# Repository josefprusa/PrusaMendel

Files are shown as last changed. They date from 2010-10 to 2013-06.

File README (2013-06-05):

Prusa Mendel iteration 2

This is second big change, formerly known as felt branch.
Released 11.11.11 :-)

Please read http://reprap.org/wiki/Prusa_Mendel before attempting to build this. There is also PDF (manual-wiki) with backup documentation from reprap.org.  

Imported stuff:
Extruder by Greg Frost
Parametric Involute Bevel and Spur Gears by GregFrost
Belt pulley is http://www.thingiverse.com/thing:3104 by GilesBathgate

Prusa Mendel part list:

To print (not including the extruder drive):

4x frame-vertex-with-foot
2x frame-vertex-without-foot
2x coupling
1x x-carriage
1x x-end-idler
1x x-end-motor
2x z-motor-mount
4x belt-clamp
2x belt-clamp-nut-holder
8x bar-clamp
2x rod-clamp
1x y-motor-bracket
3x y-bushing
3x endstop-holder

X90390893??°03I

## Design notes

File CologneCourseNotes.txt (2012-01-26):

M8 nut trap on the wade big gear is toooooo big
-> caused by the M8 nut set toooo big because of the compatibility with 5/16
--> but the wade bolts are all M8 so I need to introduce new variable in the settings

M3 nut traps in gregstruder are tooo small
-> introduce the M3 nut size for not melting in

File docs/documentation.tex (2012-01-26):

\documentclass[11pt]{article}
\usepackage[latin2]{inputenc}
\usepackage{a4wide}
\usepackage{graphicx}
\usepackage{hyperref}
\hypersetup{colorlinks=true,linkcolor=blue}
\title{Prusa Mendel iteration 2 Documentation}
\author{ThingDoc}

\begin{document}

\maketitle
\begin{center}
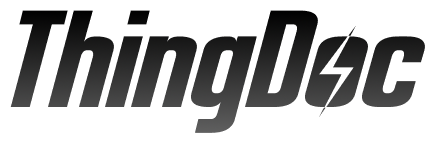
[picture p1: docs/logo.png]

\end{center}
Prusa Mendel is simplified version of Mendel form RepRap project. RepRap is open source 3D printer.

\newpage

\tableofcontents

\newpage

\section{Bill of Materials}
List of things you need to build the machine divided by categories.

\subsection{Rods and Bars}
\begin{itemize}
\item 1x \hyperlink{thing_idler-m8-piece}{Idler}
\end{itemize}

\subsection{Nuts\&bolts}
\begin{itemize}
\item 3x 608 skate bearing
\item 4x M4 nut
\item 3x M3 10mm screw
\item 2x M4 25mm screw
\item 1x \hyperlink{thing_hobbed-bolt}{M8 hobbed bolt}
\item 8x M3 15mm screw with HEX head
\item 2x M3 10mm screw with hex head
\item 1x M3 25mm screw
\item 1x M3 grub screw
\item 2x M3 25mm screw with HEX head
\item 12x M3 nut
\item 73x M8 washer
\item 74x M8 nut
\item 29x M3 washer
\item 1x M3 10mm screw with flat head
\item 2x M3 40mm screw
\end{itemize}

\subsection{Printed}
\begin{itemize}
\item 1x \hyperlink{thing_extruder-body}{Extruder body}
\item 8x \hyperlink{thing_bar-clamp}{Bar clamp}
\item 4x \hyperlink{thing_y-bushing}{Y bushing}
\item 2x \hyperlink{thing_frame-vertex}{Frame vertex}
\item 1x \hyperlink{thing_large-gear}{Large extruder gear}
\item 1x \hyperlink{thing_small-gear}{Small extruder gear}
\item 2x \hyperlink{thing_rod-clamp}{Rod clamp}
\item 4x \hyperlink{thing_frame-vertex-foot}{Frame vertex with foot}
\item 1x \hyperlink{thing_y-motor-bracket}{Y motor bracket}
\item 2x \hyperlink{thing_belt-clamp}{Belt clamp}
\item 1x \hyperlink{thing_x-carriage}{X carriage}
\item 1x \hyperlink{thing_z-motor-mount}{Z motor mount}
\item 1x \hyperlink{thing_idler}{Extruder Idler}
\end{itemize}

\newpage

\section{Things Overview}
List of things and their descriptions.

\hypertarget{thing_coupling-tube}{\subsection{Coupling tube}}
20mm long piece of PVC tube. 5mm inside diameter, 8mm outside diameter.

\hypertarget{thing_frame-triangle}{\subsection{Frame triangle}}
Two triangle parts which will later form a frame.

\hypertarget{thing_frame-with-axes}{\subsection{Frame with axes}}
Frame with all axes mounted

\hypertarget{thing_frame-vertex}{\subsection{Frame vertex}}
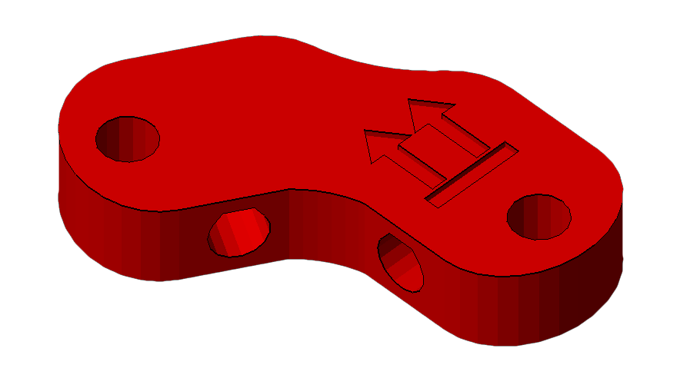
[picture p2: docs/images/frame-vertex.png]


\hypertarget{thing_frame}{\subsection{Frame}}
Frame for adding all of the other parts
There is a triangle on each side of the Prusa RepRap. You will need to make two of these and then connect them together (in the next steps) to form the Prusa frame. Each side is an equilateral triangle with a frame vertex on each corner. You can use either footed or non-footed vertices to build this. (The footed ones look better, but are not critical.) The instructions assume you are using footed vertices.

\hypertarget{thing_y-motor-bracket}{\subsection{Y motor bracket}}
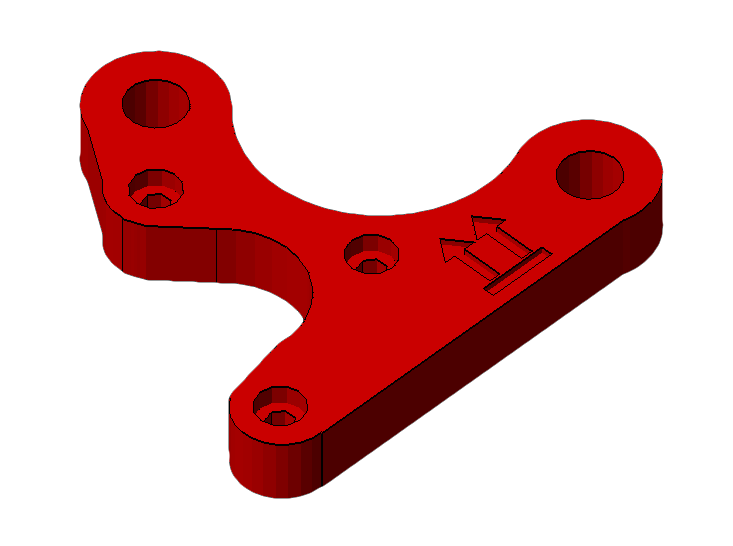
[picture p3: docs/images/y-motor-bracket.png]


\hypertarget{thing_belt-clamp}{\subsection{Belt clamp}}
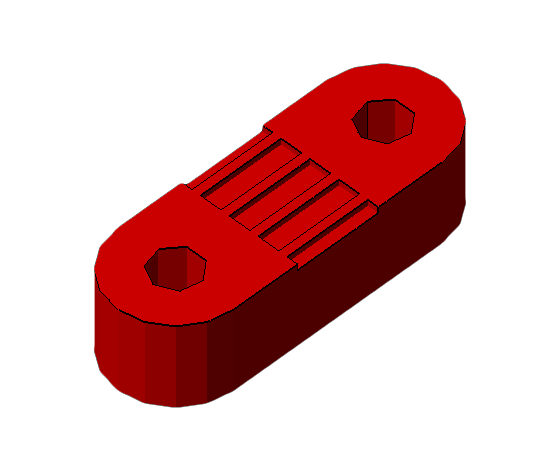
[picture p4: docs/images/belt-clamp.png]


\hypertarget{thing_hobbed-bolt}{\subsection{M8 hobbed bolt}}

\hypertarget{thing_idler}{\subsection{Extruder Idler}}
Extruder idler

\hypertarget{thing_frame-with-y}{\subsection{Frame with Y axis}}
Frame with Y axis mounted

\hypertarget{thing_y-bushing}{\subsection{Y bushing}}

\hypertarget{thing_large-gear-assembly}{\subsection{Large extruder gear assembly}}

\hypertarget{thing_bar-clamp}{\subsection{Bar clamp}}
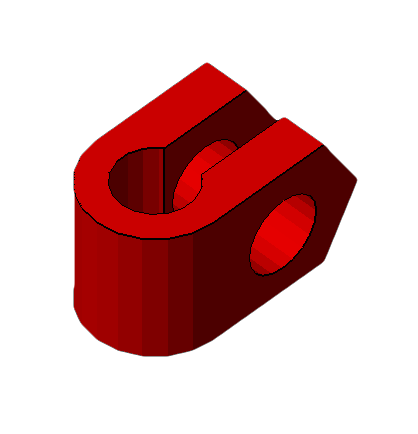
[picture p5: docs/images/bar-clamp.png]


\hypertarget{thing_xz-axis}{\subsection{XZ axis}}
Assembled XZ axis

\hypertarget{thing_large-gear}{\subsection{Large extruder gear}}

\hypertarget{thing_frame-vertex-foot}{\subsection{Frame vertex with foot}}
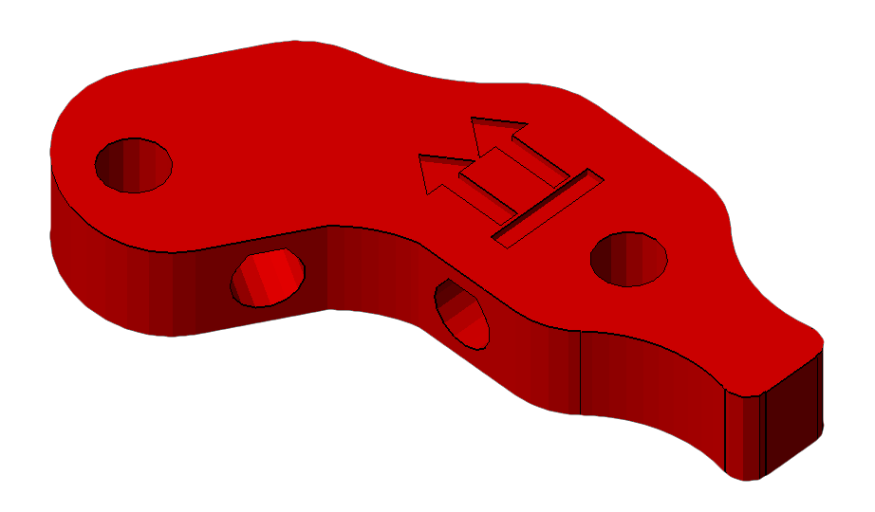
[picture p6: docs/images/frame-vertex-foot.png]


\hypertarget{thing_x-end-motor}{\subsection{X end motor}}

\hypertarget{thing_extruder-body}{\subsection{Extruder body}}
Extruder body

\hypertarget{thing_small-gear}{\subsection{Small extruder gear}}

\hypertarget{thing_extruder-spring}{\subsection{Extruder spring}}
Spring used for idler on extruder.

\hypertarget{thing_printable-bushing}{\subsection{Printable Bushing}}

\hypertarget{thing_x-carriage}{\subsection{X carriage}}
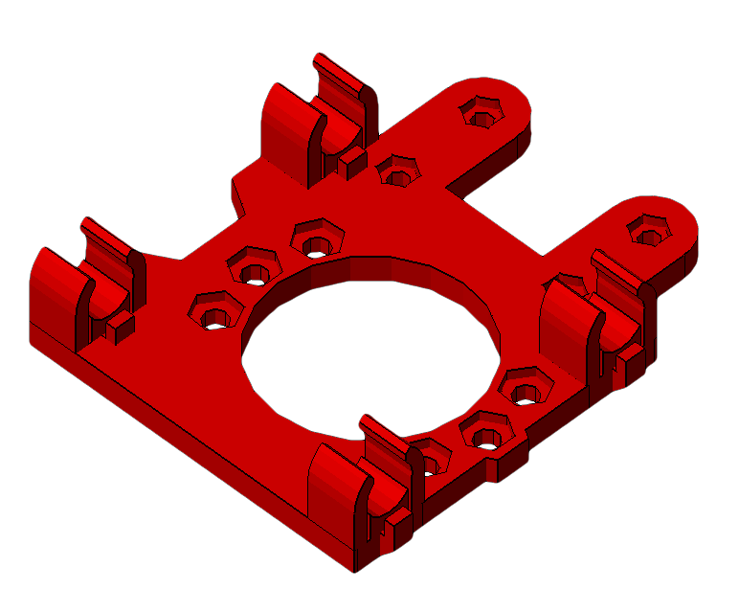
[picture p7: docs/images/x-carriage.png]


\hypertarget{thing_x-end-idler}{\subsection{X end idler}}

\hypertarget{thing_rod-clamp}{\subsection{Rod clamp}}
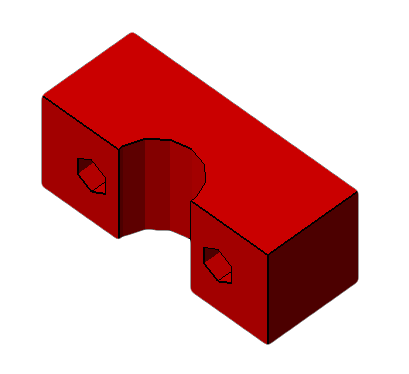
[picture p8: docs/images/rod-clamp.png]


\hypertarget{thing_z-motor-mount}{\subsection{Z motor mount}}
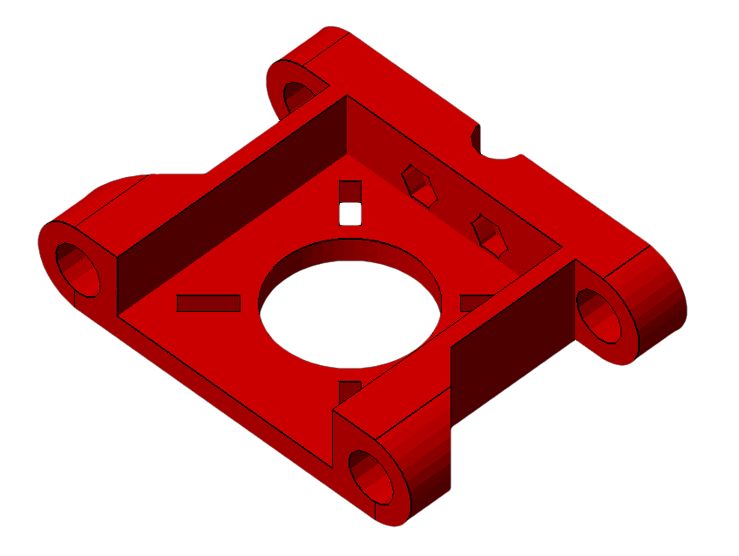
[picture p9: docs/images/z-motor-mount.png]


\hypertarget{thing_endstop-holder}{\subsection{Endstop holder}}

\hypertarget{thing_bushing}{\subsection{Bushing}}

\hypertarget{thing_idler-m8-piece}{\subsection{Idler}}
Small M8 rod

\hypertarget{thing_pulley}{\subsection{Pulley}}

\hypertarget{thing_coupling}{\subsection{Coupling}}

\hypertarget{thing_y-axis}{\subsection{Y axis}}
Assembled Y axis

\hypertarget{thing_bearing-guide}{\subsection{Bearing guide}}
Helps to hold belt aligned on the bearing.

\hypertarget{thing_cleaned-extruder-body}{\subsection{Clenaed xtruder body}}
Cleaned extruder body

\hypertarget{thing_carriage}{\subsection{Carriage}}
X-carriage with mounted extruder

\hypertarget{thing_extruder}{\subsection{Extruder}}
Extruder

\newpage

\section{Assembly Instructions}

\subsection{Assemble M8 hobbed bolt}Steps:
\begin{enumerate}
\item Use thread cutting bit in electric screwdriver ...
\end{enumerate}

\subsection{Assemble Large extruder gear assembly}
Things needed:
\begin{itemize}
\item 1x \hyperlink{thing_large-gear}{Large extruder gear}
\item 1x \hyperlink{thing_hobbed-bolt}{M8 hobbed bolt}
\end{itemize}
Steps:
\begin{enumerate}
\item Insert hobbed bolt into main hole.
\item Add some M8 washers from other side, later with their count you adjust position of hobbed part in filament path.
\end{enumerate}

\subsection{Assemble Small extruder gear}
Things needed:
\begin{itemize}
\item 1x M3 nut
\item 1x M3 grub screw
\end{itemize}
Steps:
\begin{enumerate}
\item Insert nut into cavity in printed gear.
\item Tighten the grub screw a bit, just to hold in place.
\end{enumerate}

\subsection{Assemble Clenaed xtruder body}
Things needed:
\begin{itemize}
\item 1x \hyperlink{thing_extruder-body}{Extruder body}
\end{itemize}
Steps:
\begin{enumerate}
\item Clean all the supports from the part.
\item One blocks the hole in the middle of the axis and one supports the part later making hinge for idler.
\end{enumerate}

\subsection{Assemble Extruder Idler}
Things needed:
\begin{itemize}
\item 1x 608 skate bearing
\item 1x \hyperlink{thing_idler-m8-piece}{Idler}
\end{itemize}
Steps:
\begin{enumerate}
\item Insert piece of M8 rod into bearing.
\item Insert 608 bearing with rod into printed idler part.
\end{enumerate}

\subsection{Assemble Extruder}
Things needed:
\begin{itemize}
\item 2x 608 skate bearing
\item 2x M4 nut
\item 3x M3 10mm screw
\item 1x \hyperlink{thing_large-gear-assembly}{Large extruder gear assembly}
\item 1x NEMA17 stepper motor
\item 1x \hyperlink{thing_small-gear}{Small extruder gear}
\item 1x \hyperlink{thing_cleaned-extruder-body}{Clenaed xtruder body}
\item 2x M3 40mm screw
\item 8x M3 washer
\item 1x M8 washer
\item 1x \hyperlink{thing_idler}{Extruder Idler}
\item 1x M3 nut
\item 1x M3 25mm screw
\item 2x \hyperlink{thing_extruder-spring}{Extruder spring}
\item 2x M8 nut
\end{itemize}
Steps:
\begin{enumerate}
\item Take idler and insert nut into small nut-trap inside the hinge.
\item While holding the nut in place, preprare M3x25 bolt with washer and screw it into the hinge just enough to hold the nut.
\item Now take the extruder body and idler. Place idler on the hinge counterpart and compleately screw the M3x25 bolt. This will create secured hinge.
\item Place M4 nuts into their nut traps, secure them with piece of tape. We need them in place, since later they would be harder to access.
\item Prepare your NEMA17 stepper motor and three M3x10 screws with washers.
\item Hold motor on place and lightly tighten the screws. We need to adjust motor position later, no need to tighten it hard.
\item Place two skate bearings on ther position, they should snuggly fit in.
\item Insert prepared large gear into the body with mounted bearings.
\item Check if the alignment of hobbed part with the filament path. Adjust it accordingly with adding or removing M8 washers.
\item After adjusting, we need to fix the bolt in. So we place washer at the end of hobbed bolt and with two M8 nuts we will do locknut by tightening them against each other.
\item Check if large gear turns freely.
\item Prepare two M3x40 screws with sandwitch of washer-spring-washer.
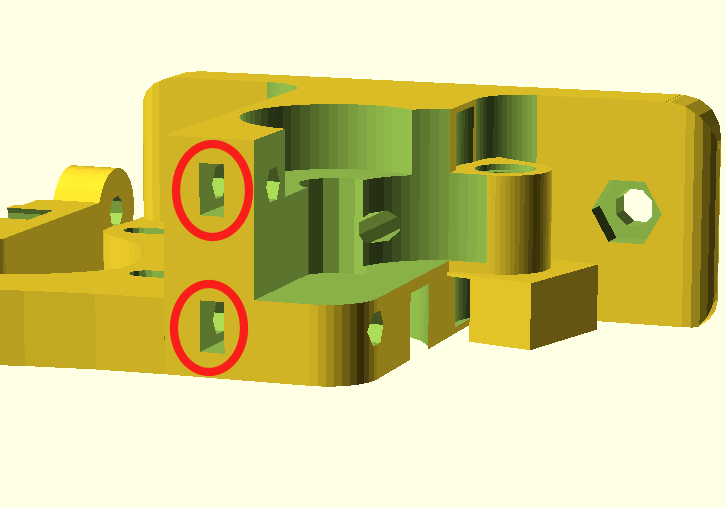
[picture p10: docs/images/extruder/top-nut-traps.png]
\item Insert two M3 nuts into nut traps on top of drive mechanism.\\ 
\item Insert prepared screws into the holes on idler. Close the idler and tighten the screws into the trapped nuts. More you tighten those screws, more pressure will be on fillament.
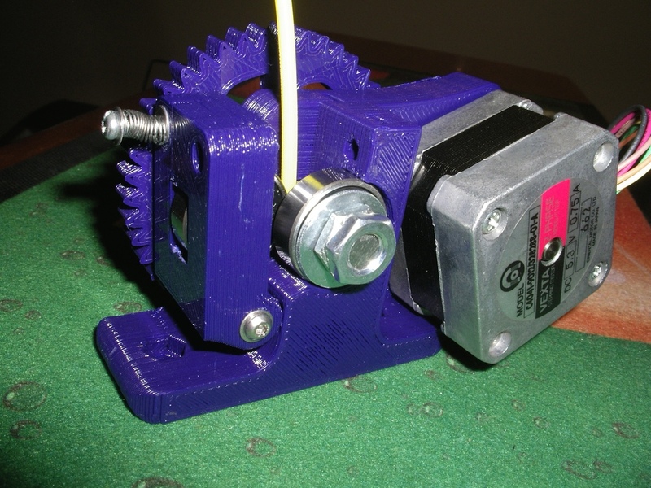
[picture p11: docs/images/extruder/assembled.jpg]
\item Your extruder is done.\\ 
\end{enumerate}

\subsection{Assemble Frame triangle}
Things needed:
\begin{itemize}
\item 1x \hyperlink{thing_bar-clamp}{Bar clamp}
\item 1x \hyperlink{thing_frame-vertex}{Frame vertex}
\item 2x \hyperlink{thing_frame-vertex-foot}{Frame vertex with foot}
\end{itemize}
Steps:
\begin{enumerate}
\item Take one of the 370mm threaded rods, and slip an M8 washer onto the middle of it.
\item Take the RP bar clamp (the U-shaped bit with the two holes) and slide the threaded rod through the two holes until the clamp sits next to the washer.
\item Slide another washer onto the rod from the other side.
\item Thread two M8 nuts onto either side of the clamp, until they are next to the washer, but do not tighten them yet.
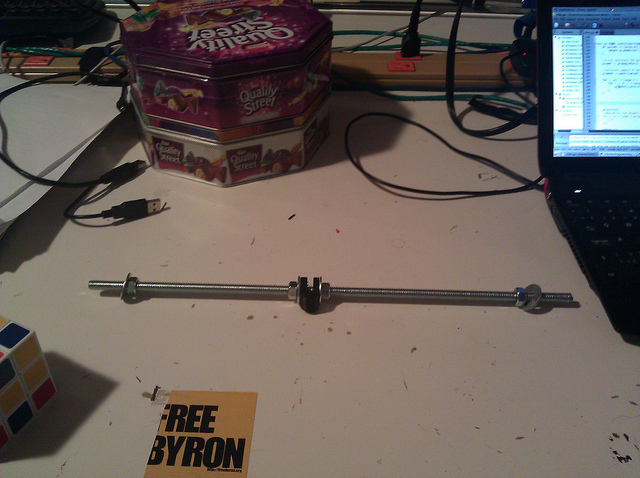
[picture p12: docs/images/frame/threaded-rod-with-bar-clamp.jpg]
\item Thread another two nuts on each side of the rod, followed by washers. See the picture for what it should look like.\\ 
\item The bar clamp on the threaded rod.
\item Slide the rod through the wider bottom (footed) side of two vertices. Make sure the feet point in the same direction, and the bulge on the non-footed sides of the vertices point outwards.
\item Place another washer and nut on the other side of the vertex. Tighten, but not too much. We'll need a bit of flexibility here still.
\item Take another 370mm M8 threaded rod and place a nut followed by a washer at each end.
\item Place one end of the threaded rod into the one of the two footed frame vertices. It should be in the same plane as the first threaded rod. Fix it in place with a washer and nut. You should now have two sides of the equilateral triangle.
\item Take the third piece of threaded rod and put a nut and washer on each end. Place it in the other footed vertex and fix it in place with a washer and nut. You should now have a triangle of threaded rods with two footed vertices on two of the corners, nothing in the third corner, and a bar clamp between the two vertices.
\item Take the third vertex (non-footed) and slide it onto the threaded rods in the final corner of the triangle.
\item Move all the nuts on the end of the rods to the exact end of the rod. Tighten all the inner nuts. This way, no measurement is needed.
\item You should now have a sturdy triangle with equal-length sides, two feet on the bottom, and a bar clamp between the feet. Adjust the nuts around the bar clamp (but do not crush the bar clamp together yet) until it's approximately in the middle of the rod. Leave the nuts there loose. See the photo for what you should have at this point.
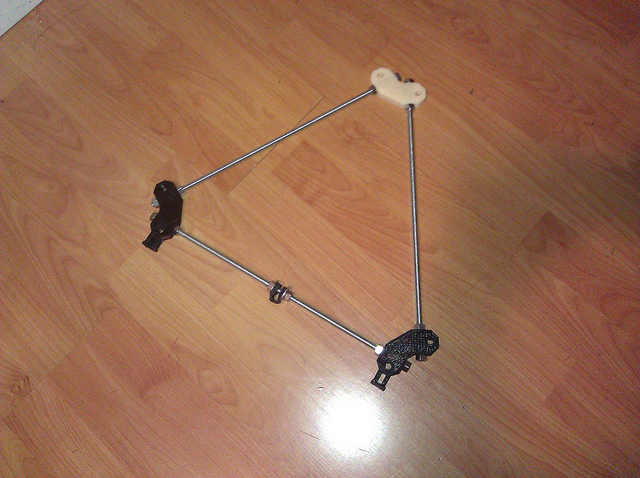
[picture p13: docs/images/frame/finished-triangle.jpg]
\item That's it, that's one of the triangles done. Repeat the entire procedure for the second triangle. It is identical to the first.\\ 
\end{enumerate}

\subsection{Assemble Prusa Mendel iteration 2}
Things needed:
\begin{itemize}
\item 1x \hyperlink{thing_carriage}{Carriage}
\item 1x \hyperlink{thing_frame-with-axes}{Frame with axes}
\end{itemize}
Steps:
\begin{enumerate}
\item Assembly info
\end{enumerate}

\newpage

\end{document}

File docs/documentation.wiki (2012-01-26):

== Bill of Materials ==

=== Rods and Bars ===
{| class="wikitable sortable" border="1"
|-
! scope="col" | Quantity
! scope="col" | Description
! scope="col" | Type
! scope="col" class="unsortable" | Comments
! scope="col" class="unsortable" | Diagram
|-
| 1 || Idler ||  ||  ||
|}

=== Nuts&bolts ===
{| class="wikitable sortable" border="1"
|-
! scope="col" | Quantity
! scope="col" | Description
! scope="col" | Type
! scope="col" class="unsortable" | Comments
! scope="col" class="unsortable" | Diagram
|-
| 3 || 608 skate bearing ||  ||  || 50px
|-
| 4 || M4 nut ||  ||  ||
|-
| 3 || M3 10mm screw ||  ||  ||
|-
| 2 || M4 25mm screw ||  ||  ||
|-
| 1 || M8 hobbed bolt ||  ||  ||
|-
| 8 || M3 15mm screw with HEX head ||  ||  ||
|-
| 2 || M3 10mm screw with hex head ||  ||  ||
|-
| 1 || M3 25mm screw ||  ||  ||
|-
| 1 || M3 grub screw ||  ||  ||
|-
| 2 || M3 25mm screw with HEX head ||  ||  ||
|-
| 12 || M3 nut ||  ||  ||
|-
| 73 || M8 washer ||  ||  ||
|-
| 74 || M8 nut ||  ||  ||
|-
| 29 || M3 washer ||  ||  ||
|-
| 1 || M3 10mm screw with flat head ||  ||  ||
|-
| 2 || M3 40mm screw ||  ||  ||
|}

=== Printed ===
{| class="wikitable sortable" border="1"
|-
! scope="col" | Quantity
! scope="col" | Description
! scope="col" | Type
! scope="col" class="unsortable" | Comments
! scope="col" class="unsortable" | Diagram
|-
| 1 || Extruder body ||  ||  ||
|-
| 8 || Bar clamp ||  ||  || 50px
|-
| 4 || Y bushing ||  ||  ||
|-
| 2 || Frame vertex ||  ||  || 50px
|-
| 1 || Large extruder gear ||  ||  ||
|-
| 1 || Small extruder gear ||  ||  ||
|-
| 2 || Rod clamp ||  ||  || 50px
|-
| 4 || Frame vertex with foot ||  ||  || 50px
|-
| 1 || Y motor bracket ||  ||  || 50px
|-
| 2 || Belt clamp ||  ||  || 50px
|-
| 1 || X carriage ||  ||  || 50px
|-
| 1 || Z motor mount ||  ||  || 50px
|-
| 1 || Extruder Idler ||  ||  ||
|}

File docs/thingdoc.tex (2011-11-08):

\documentclass[11pt]{article}
\usepackage[latin2]{inputenc}
\usepackage{a4wide}
\usepackage{graphicx}
\usepackage{hyperref}
\hypersetup{colorlinks=true,linkcolor=blue}
\title{Prusa Mendel generation 2 Documentation}
\author{ThingDoc}

\begin{document}

\maketitle
\begin{center}

\end{center}
Prusa Mendel is simplified version of Mendel form RepRap project. RepRap is open source 3D printer.

\newpage

\tableofcontents

\newpage

\section{Bill of Materials}
List of things you need to build the machine divided by categories.

\subsection{Rods and Bars}
\begin{itemize}
\item 1x \hyperlink{thing_idler-m8-piece}{Idler}
\end{itemize}

\subsection{Nuts\&bolts}
\begin{itemize}
\item 3x 608 skate bearing
\item 4x M4 nut
\item 3x M3 10mm screw
\item 2x M4 25mm screw
\item 1x \hyperlink{thing_hobbed-bolt}{M8 hobbed bolt}
\item 8x M3 15mm screw with HEX head
\item 2x M3 10mm screw with hex head
\item 1x M3 25mm screw
\item 1x M3 grub screw
\item 2x M3 25mm screw with HEX head
\item 12x M3 nut
\item 73x M8 washer
\item 74x M8 nut
\item 29x M3 washer
\item 1x M3 10mm screw with flat head
\item 2x M3 40mm screw
\end{itemize}

\subsection{Printed}
\begin{itemize}
\item 1x \hyperlink{thing_extruder-body}{Extruder body}
\item 8x \hyperlink{thing_bar-clamp}{Bar clamp}
\item 4x \hyperlink{thing_y-bushing}{Y bushing}
\item 2x \hyperlink{thing_frame-vertex}{Frame vertex}
\item 1x \hyperlink{thing_y-motor-bracket}{Y motor bracket}
\item 1x \hyperlink{thing_small-gear}{Small extruder gear}
\item 2x \hyperlink{thing_rod-clamp}{Rod clamp}
\item 4x \hyperlink{thing_frame-vertex-foot}{Frame vertex with foot}
\item 1x \hyperlink{thing_large-gear}{Large extruder gear}
\item 2x \hyperlink{thing_belt-clamp}{Belt clamp}
\item 1x \hyperlink{thing_idler}{Extruder Idler}
\item 1x \hyperlink{thing_z-motor-mount}{Z motor mount}
\item 1x \hyperlink{thing_x-carriage}{X carriage}
\end{itemize}

\newpage

\section{Things Overview}
List of things and their descriptions.

\hypertarget{thing_coupling-tube}{\subsection{Coupling tube}}
20mm long piece of PVC tube. 5mm inside diameter, 8mm outside diameter.

\hypertarget{thing_frame-triangle}{\subsection{Frame triangle}}
Two triangle parts which will later form a frame.

\hypertarget{thing_y-axis}{\subsection{Y axis}}
Assembled Y axis

\hypertarget{thing_frame-with-axes}{\subsection{Frame with axes}}
Frame with all axes mounted

\hypertarget{thing_frame-vertex}{\subsection{Frame vertex}}


\hypertarget{thing_frame}{\subsection{Frame}}
Frame for adding all of the other parts
There is a triangle on each side of the Prusa RepRap. You will need to make two of these and then connect them together (in the next steps) to form the Prusa frame. Each side is an equilateral triangle with a frame vertex on each corner. You can use either footed or non-footed vertices to build this. (The footed ones look better, but are not critical.) The instructions assume you are using footed vertices.

\hypertarget{thing_y-motor-bracket}{\subsection{Y motor bracket}}


\hypertarget{thing_belt-clamp}{\subsection{Belt clamp}}


\hypertarget{thing_hobbed-bolt}{\subsection{M8 hobbed bolt}}

\hypertarget{thing_idler}{\subsection{Extruder Idler}}
Extruder idler

\hypertarget{thing_frame-with-y}{\subsection{Frame with Y axis}}
Frame with Y axis mounted

\hypertarget{thing_y-bushing}{\subsection{Y bushing}}

\hypertarget{thing_bar-clamp}{\subsection{Bar clamp}}


\hypertarget{thing_calibration}{\subsection{Configuration test}}

\hypertarget{thing_xz-axis}{\subsection{XZ axis}}
Assembled XZ axis

\hypertarget{thing_large-gear}{\subsection{Large extruder gear}}

\hypertarget{thing_frame-vertex-foot}{\subsection{Frame vertex with foot}}

\hypertarget{thing_x-end-motor}{\subsection{X end motor}}

\hypertarget{thing_extruder-body}{\subsection{Extruder body}}
Extruder body

\hypertarget{thing_small-gear}{\subsection{Small extruder gear}}

\hypertarget{thing_extruder-spring}{\subsection{Extruder spring}}
Spring used for idler on extruder.

\hypertarget{thing_printable-bushing}{\subsection{Printable Bushing}}

\hypertarget{thing_x-carriage}{\subsection{X carriage}}


\hypertarget{thing_x-end-idler}{\subsection{X end idler}}

\hypertarget{thing_rod-clamp}{\subsection{Rod clamp}}


\hypertarget{thing_z-motor-mount}{\subsection{Z motor mount}}


\hypertarget{thing_endstop-holder}{\subsection{Endstop holder}}

\hypertarget{thing_bushing}{\subsection{Bushing}}

\hypertarget{thing_idler-m8-piece}{\subsection{Idler}}
Small M8 rod

\hypertarget{thing_pulley}{\subsection{Pulley}}

\hypertarget{thing_coupling}{\subsection{Coupling}}

\hypertarget{thing_bearing-guide}{\subsection{Bearing guide}}
Helps to hold belt aligned on the bearing.

\hypertarget{thing_carriage}{\subsection{Carriage}}
X-carriage with mounted extruder

\hypertarget{thing_extruder}{\subsection{Extruder}}
Extruder

\newpage

\section{Assembly Instructions}

\subsection{Assemble Small extruder gear}
Things needed:
\begin{itemize}
\item 1x M3 nut
\item 1x M3 grub screw
\end{itemize}
Steps:
\begin{enumerate}
\item Insert nut into cavity in printed gear.
\item Tighten the grub screw a bit, just to hold in place.
\end{enumerate}

\subsection{Assemble M8 hobbed bolt}Steps:
\begin{enumerate}
\item Use thread cutting bit in electric screwdriver ...
\end{enumerate}

\subsection{Assemble Large extruder gear}
Things needed:
\begin{itemize}
\item 1x \hyperlink{thing_hobbed-bolt}{M8 hobbed bolt}
\end{itemize}
Steps:
\begin{enumerate}
\item Insert hobbed bolt into main hole.
\item Add some M8 washers from other side, later with their count you adjust position of hobbed part in filament path.
\end{enumerate}

\subsection{Assemble Extruder Idler}
Things needed:
\begin{itemize}
\item 1x 608 skate bearing
\item 1x \hyperlink{thing_idler-m8-piece}{Idler}
\end{itemize}
Steps:
\begin{enumerate}
\item Insert piece of M8 rod into bearing.
\item Insert 608 bearing with rod into printed idler part.
\end{enumerate}

\subsection{Assemble Extruder}
Things needed:
\begin{itemize}
\item 2x 608 skate bearing
\item 1x \hyperlink{thing_extruder-body}{Extruder body}
\item 3x M3 10mm screw
\item 2x M4 nut
\item 1x \hyperlink{thing_small-gear}{Small extruder gear}
\item 1x M3 25mm screw
\item 1x NEMA17 stepper motor
\item 1x \hyperlink{thing_large-gear}{Large extruder gear}
\item 8x M3 washer
\item 1x M8 washer
\item 1x \hyperlink{thing_idler}{Extruder Idler}
\item 1x M3 nut
\item 2x M3 40mm screw
\item 2x \hyperlink{thing_extruder-spring}{Extruder spring}
\item 2x M8 nut
\end{itemize}
Steps:
\begin{enumerate}
\item Take idler and insert nut into small nut-trap inside the hinge.
\item While holding the nut in place, preprare M3x25 bolt with washer and screw it into the hinge just enough to hold the nut.
\item Now take the extruder body and idler. Place idler on the hinge counterpart and compleately screw the M3x25 bolt. This will create secured hinge.
\item Place M4 nuts into their nut traps, secure them with piece of tape. We need them in place, since later they would be harder to access.
\item Prepare your NEMA17 stepper motor and three M3x10 screws with washers.
\item Hold motor on place and lightly tighten the screws. We need to adjust motor position later, no need to tighten it hard.
\item Place two skate bearings on ther position, they should snuggly fit in.
\item Insert prepared large gear into the body with mounted bearings.
\item Check if the alignment of hobbed part with the filament path. Adjust it accordingly with adding or removing M8 washers.
\item After adjusting, we need to fix the bolt in. So we place washer at the end of hobbed bolt and with two M8 nuts we will do locknut by tightening them against each other.
\item Check if large gear turns freely.
\item Prepare two M3x40 screws with sandwitch of washer-spring-washer.
\item Insert two M3 nuts into nut traps on top of drive mechanism.\\ 
\item Insert prepared screws into the holes on idler. Close the idler and tighten the screws into the trapped nuts. More you tighten those screws, more pressure will be on fillament.
\item Your extruder is done.\\ 
\end{enumerate}

\subsection{Assemble Frame triangle}
Things needed:
\begin{itemize}
\item 1x \hyperlink{thing_bar-clamp}{Bar clamp}
\item 1x \hyperlink{thing_frame-vertex}{Frame vertex}
\item 2x \hyperlink{thing_frame-vertex-foot}{Frame vertex with foot}
\end{itemize}
Steps:
\begin{enumerate}
\item Take one of the 370mm threaded rods, and slip an M8 washer onto the middle of it.
\item Take the RP bar clamp (the U-shaped bit with the two holes) and slide the threaded rod through the two holes until the clamp sits next to the washer.
\item Slide another washer onto the rod from the other side.
\item Thread two M8 nuts onto either side of the clamp, until they are next to the washer, but do not tighten them yet.
\item Thread another two nuts on each side of the rod, followed by washers. See the picture for what it should look like.\\ 
\item The bar clamp on the threaded rod.
\item Slide the rod through the wider bottom (footed) side of two vertices. Make sure the feet point in the same direction, and the bulge on the non-footed sides of the vertices point outwards.
\item Measure the distance. The distance between the two vertices should be 290mm (along the rod, equivalent is 11-13/32"). Get it approximately right now, we will check this again later. If you have a frame jig, place it between the two vertices and adjust the nuts until you can just barely fit the jig J1 between them.
\item Place another washer and nut on the other side of the vertex. Tighten, but not too much. We'll need a bit of flexibility here still.
\item Take another 370mm M8 threaded rod and place a nut followed by a washer at each end.
\item Place one end of the threaded rod into the one of the two footed frame vertices. It should be in the same plane as the first threaded rod. Fix it in place with a washer and nut. You should now have two sides of the equilateral triangle.
\item Take the third piece of threaded rod and put a nut and washer on each end. Place it in the other footed vertex and fix it in place with a washer and nut. You should now have a triangle of threaded rods with two footed vertices on two of the corners, nothing in the third corner, and a bar clamp between the two vertices.
\item Take the third vertex (non-footed) and slide it onto the threaded rods in the final corner of the triangle. Measure the lengths of the three sides to make sure they are all 290mm long (along the rod from plastic part to plastic part, equivalent is 11-13/32"). Adjust the nuts to make sure this is so. Use the frame jig J1 if you have one. Once done, place a washer and nut on each of the two rods at the top of the vertex. Tighten all the outer nuts.
\item The finished frame triangle
\item You should now have a sturdy triangle with equal-length sides, two feet on the bottom, and a bar clamp between the feet. Adjust the nuts around the bar clamp (but do not crush the bar clamp together yet) until it's approximately in the middle of the rod. Leave the nuts there loose. See the photo for what you should have at this point.
\item That's it, that's one of the triangles done. Repeat the entire procedure for the second triangle. It is identical to the first.\\ 
\end{enumerate}

\subsection{Assemble Prusa Mendel generation 2}
Things needed:
\begin{itemize}
\item 1x \hyperlink{thing_carriage}{Carriage}
\item 1x \hyperlink{thing_frame-with-axes}{Frame with axes}
\end{itemize}
Steps:
\begin{enumerate}
\item Assembly info
\end{enumerate}

\newpage

\end{document}

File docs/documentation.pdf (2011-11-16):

## Prusa Mendel iteration 2 Documentation

ThingDoc

November 16, 2011

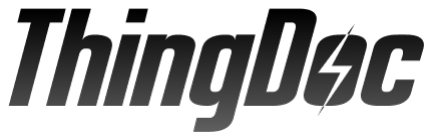
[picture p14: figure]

Prusa Mendel is simplified version of Mendel form RepRap project. RepRap is open source 3D printer.

## Contents

## 1 Bill of Materials

List of things you need to build the machine divided by categories.

### 1.1 Rods and Bars

- 1x Idler

### 1.2 Nuts&bolts

- 3x 608 skate bearing
- 4x M4 nut
- 3x M3 10mm screw
- 2x M4 25mm screw
- 1x M8 hobbed bolt
- 8x M3 15mm screw with HEX head
- 2x M3 10mm screw with hex head
- 1x M3 25mm screw
- 1x M3 grub screw
- 2x M3 25mm screw with HEX head
- 12x M3 nut
- 73x M8 washer
- 74x M8 nut
- 29x M3 washer
- 1x M3 10mm screw with flat head
- 2x M3 40mm screw

### 1.3 Printed

- 1x Extruder body
- 8x Bar clamp
- 4x Y bushing
- 2x Frame vertex
- 1x Y motor bracket
- 1x Small extruder gear

- 2x Rod clamp
- 4x Frame vertex with foot
- 1x Large extruder gear
- 2x Belt clamp
- 1x Extruder Idler
- 1x Z motor mount
- 1x X carriage

## 2 Things Overview

List of things and their descriptions.

### 2.1 Coupling tube

20mm long piece of PVC tube. 5mm inside diameter, 8mm outside diameter.

### 2.2 Frame triangle

Two triangle parts which will later form a frame.

### 2.3 Frame with axes

Frame with all axes mounted

### 2.4 Frame vertex

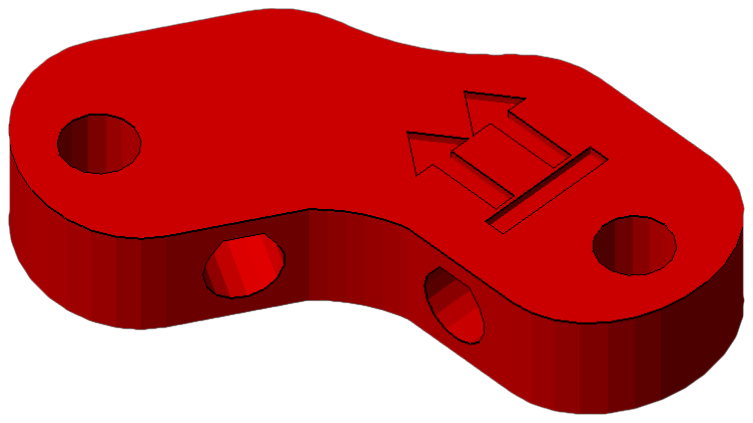
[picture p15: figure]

### 2.5 Frame

Frame for adding all of the other parts There is a triangle on each side of the Prusa RepRap. You will need to make two of these and then connect them together (in the next steps) to form the Prusa frame. Each side is an equilateral triangle with a frame vertex on each corner. You can use either footed or non-footed vertices to build this. (The footed ones look better, but are not critical.) The instructions assume you are using footed vertices.

### 2.6 Y motor bracket

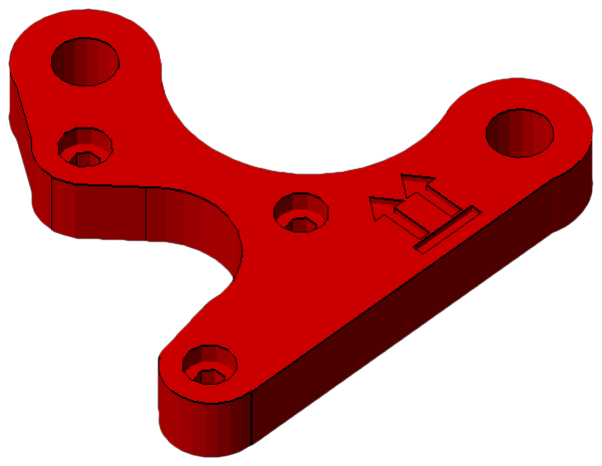
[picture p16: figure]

### 2.7 Belt clamp

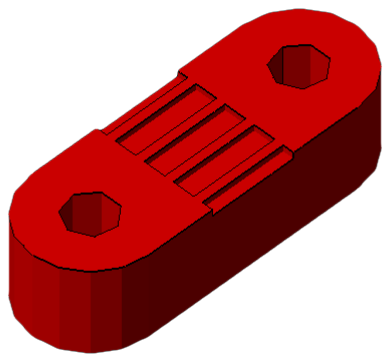
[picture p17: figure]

### 2.8 M8 hobbed bolt

### 2.9 Extruder Idler

Extruder idler

### 2.10 Frame with Y axis

Frame with Y axis mounted

### 2.11 Y bushing

### 2.12 Bar clamp

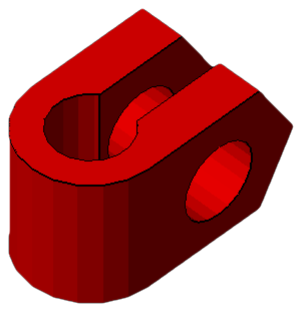
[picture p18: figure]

### 2.13 XZ axis

Assembled XZ axis

### 2.14 Large extruder gear

### 2.15 Frame vertex with foot

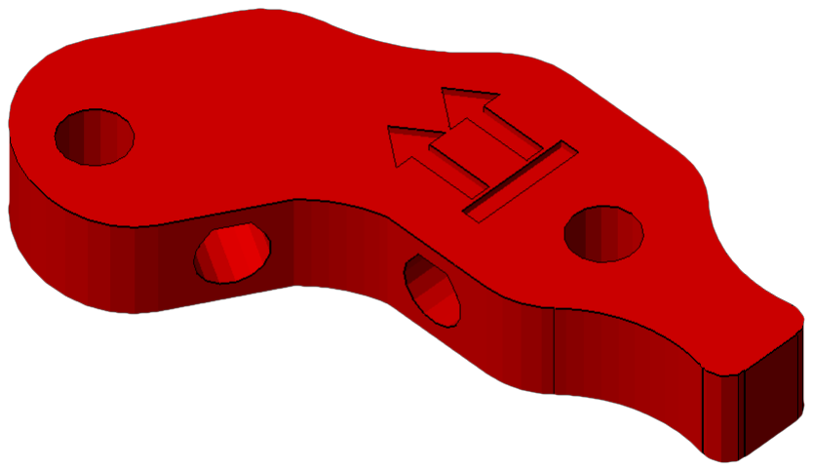
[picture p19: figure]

### 2.16 X end motor

### 2.17 Extruder body

Extruder body

### 2.18 Small extruder gear

### 2.19 Extruder spring

Spring used for idler on extruder.

### 2.20 Printable Bushing

### 2.21 X carriage

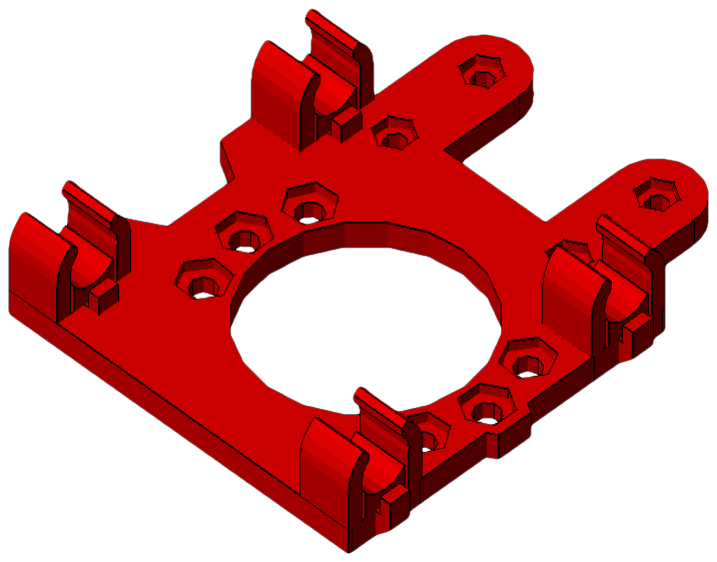
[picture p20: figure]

### 2.22 X end idler

### 2.23 Rod clamp

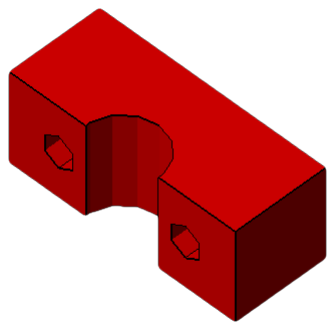
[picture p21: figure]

### 2.24 Z motor mount

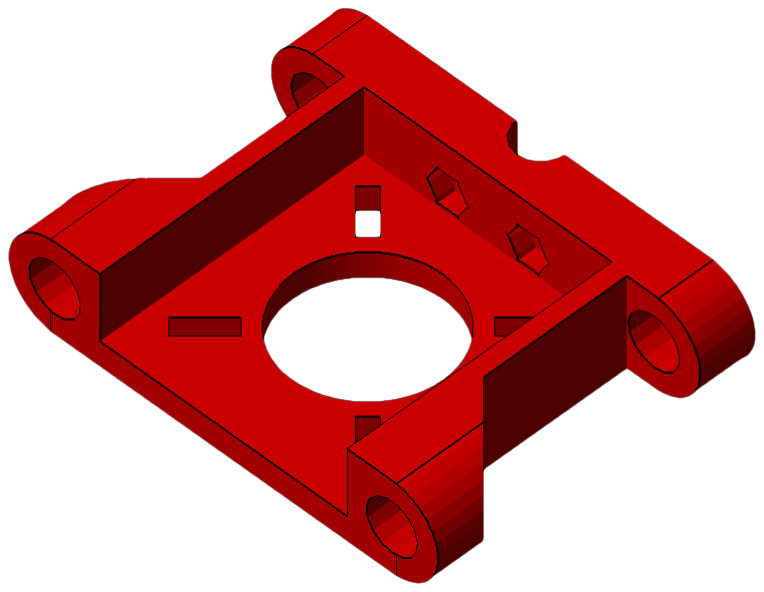
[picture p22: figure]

### 2.25 Endstop holder

### 2.26 Bushing

### 2.27 Idler

Small M8 rod

### 2.28 Pulley

### 2.29 Coupling

### 2.30 Y axis

Assembled Y axis

### 2.31 Bearing guide

Helps to hold belt aligned on the bearing.

### 2.32 Carriage

X-carriage with mounted extruder

### 2.33 Extruder

Extruder

## 3 Assembly Instructions

### 3.1 Assemble Small extruder gear

Things needed:

- 1x M3 nut
- 1x M3 grub screw

Steps:

1. Insert nut into cavity in printed gear.
2. Tighten the grub screw a bit, just to hold in place.

### 3.2 Assemble M8 hobbed bolt

Steps:

1. Use thread cutting bit in electric screwdriver ...

### 3.3 Assemble Large extruder gear

Things needed:

- 1x M8 hobbed bolt

Steps:

1. Insert hobbed bolt into main hole.
2. Add some M8 washers from other side, later with their count you adjust position of hobbed part in filament path.

### 3.4 Assemble Extruder Idler

Things needed:

- 1x 608 skate bearing
- 1x Idler

Steps:

1. Insert piece of M8 rod into bearing.
2. Insert 608 bearing with rod into printed idler part.

### 3.5 Assemble Extruder

Things needed:

- 2x 608 skate bearing
- 1x Extruder body
- 3x M3 10mm screw
- 2x M4 nut
- 1x Small extruder gear
- 1x M3 25mm screw
- 1x NEMA17 stepper motor
- 1x Large extruder gear
- 8x M3 washer
- 1x M8 washer
- 1x Extruder Idler
- 1x M3 nut
- 2x M3 40mm screw
- 2x Extruder spring
- 2x M8 nut

Steps:

1. Take idler and insert nut into small nut-trap inside the hinge.
2. While holding the nut in place, preprare M3x25 bolt with washer and screw it into the hinge just enough to hold the nut.
3. Now take the extruder body and idler. Place idler on the hinge counterpart and com-pleately screw the M3x25 bolt. This will create secured hinge.
4. Place M4 nuts into their nut traps, secure them with piece of tape. We need them in place, since later they would be harder to access.
5. Prepare your NEMA17 stepper motor and three M3x10 screws with washers.
6. Hold motor on place and lightly tighten the screws. We need to adjust motor position later, no need to tighten it hard.
7. Place two skate bearings on ther position, they should snuggly fit in.
8. Insert prepared large gear into the body with mounted bearings.

9. Check if the alignment of hobbed part with the filament path. Adjust it accordingly with adding or removing M8 washers.
10. After adjusting, we need to fix the bolt in. So we place washer at the end of hobbed bolt and with two M8 nuts we will do locknut by tightening them against each other.
11. Check if large gear turns freely.
12. Prepare two M3x40 screws with sandwitch of washer-spring-washer.
13. Insert two M3 nuts into nut traps on top of drive mechanism.


14. Insert prepared screws into the holes on idler. Close the idler and tighten the screws into the trapped nuts. More you tighten those screws, more pressure will be on fillament.
15. Your extruder is done.


### 3.6 Assemble Frame triangle

Things needed:

- 1x Bar clamp
- 1x Frame vertex
- 2x Frame vertex with foot

Steps:

1. Take one of the 370mm threaded rods, and slip an M8 washer onto the middle of it.
2. Take the RP bar clamp (the U-shaped bit with the two holes) and slide the threaded rod through the two holes until the clamp sits next to the washer.
3. Slide another washer onto the rod from the other side.
4. Thread two M8 nuts onto either side of the clamp, until they are next to the washer, but do not tighten them yet.

5. Thread another two nuts on each side of the rod, followed by washers. See the picture for what it should look like.


6. The bar clamp on the threaded rod.
7. Slide the rod through the wider bottom (footed) side of two vertices. Make sure the feet point in the same direction, and the bulge on the non-footed sides of the vertices point outwards.
8. Measure the distance. The distance between the two vertices should be 290mm (along the rod, equivalent is 11-13/32”). Get it approximately right now, we will check this again later. If you have a frame jig, place it between the two vertices and adjust the nuts until you can just barely fit the jig J1 between them.
9. Place another washer and nut on the other side of the vertex. Tighten, but not too much. We’ll need a bit of flexibility here still.
10. Take another 370mm M8 threaded rod and place a nut followed by a washer at each end.
11. Place one end of the threaded rod into the one of the two footed frame vertices. It should be in the same plane as the first threaded rod. Fix it in place with a washer and nut. You should now have two sides of the equilateral triangle.
12. Take the third piece of threaded rod and put a nut and washer on each end. Place it in the other footed vertex and fix it in place with a washer and nut. You should now have a triangle of threaded rods with two footed vertices on two of the corners, nothing in the third corner, and a bar clamp between the two vertices.
13. Take the third vertex (non-footed) and slide it onto the threaded rods in the final corner of the triangle. Measure the lengths of the three sides to make sure they are all 290mm long (along the rod from plastic part to plastic part, equivalent is 11-13/32”). Adjust the nuts to make sure this is so. Use the frame jig J1 if you have one. Once done, place a washer and nut on each of the two rods at the top of the vertex. Tighten all the outer nuts.
14. The finished frame triangle
15. You should now have a sturdy triangle with equal-length sides, two feet on the bottom, and a bar clamp between the feet. Adjust the nuts around the bar clamp (but do not crush the bar clamp together yet) until it’s approximately in the middle of the rod. Leave the nuts there loose. See the photo for what you should have at this point.

16. That’s it, that’s one of the triangles done. Repeat the entire procedure for the second triangle. It is identical to the first.


### 3.7 Assemble Prusa Mendel iteration 2

Things needed:

- 1x Carriage
- 1x Frame with axes

Steps:

1. Assembly info

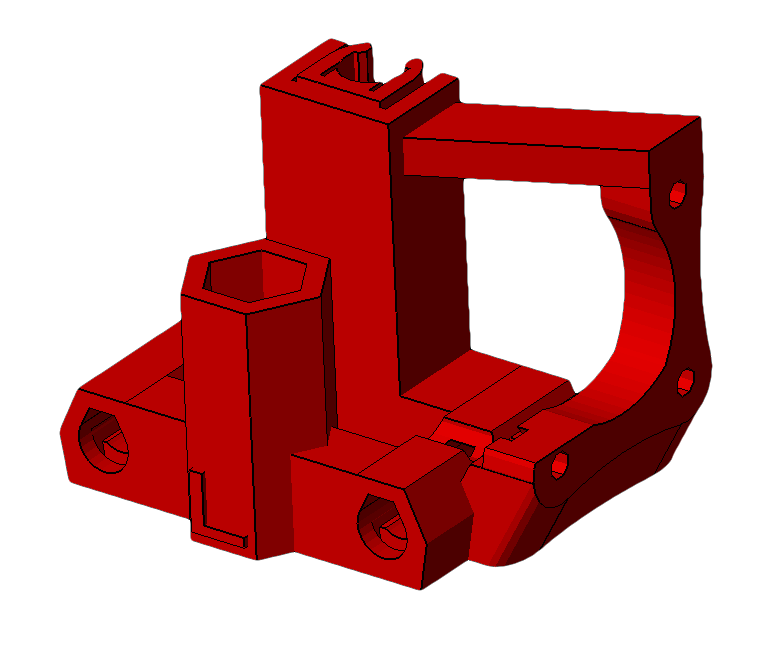
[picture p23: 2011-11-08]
docs/images/x-end-motor.png

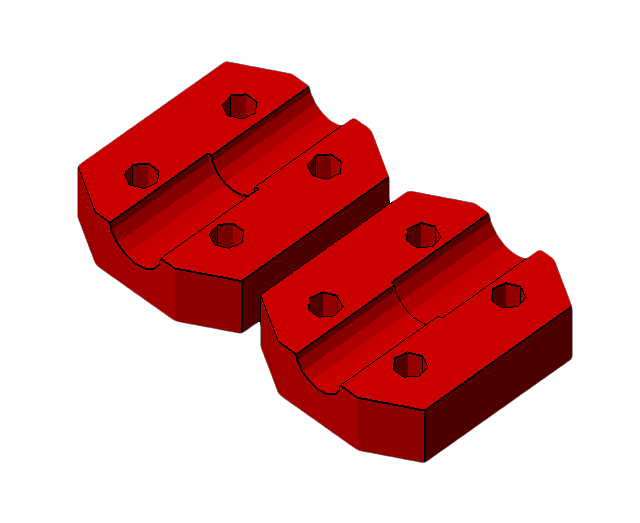
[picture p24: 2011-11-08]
docs/images/coupling.png

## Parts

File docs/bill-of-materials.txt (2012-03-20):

Bill of Materials: Prusa Mendel iteration 2
+++++++++++++++++++++++++++++++++++++++++++

Rods and Bars
=============
- 1x Idler 

Nuts&bolts
==========
- 3x 608 skate bearing
- 4x M4 nut
- 3x M3 10mm screw
- 2x M4 25mm screw
- 1x M8 hobbed bolt
- 8x M3 15mm screw with HEX head
- 2x M3 10mm screw with hex head
- 1x M3 25mm screw
- 1x M3 grub screw
- 2x M3 25mm screw with HEX head
- 12x M3 nut
- 73x M8 washer
- 74x M8 nut
- 29x M3 washer
- 1x M3 10mm screw with flat head
- 2x M3 40mm screw

Printed
=======
- 1x Extruder body
- 8x Bar clamp
- 4x Y bushing
- 2x Frame vertex
- 1x Large extruder gear
- 1x Small extruder gear
- 2x Rod clamp
- 4x Frame vertex with foot
- 1x Y motor bracket
- 4x Belt clamp
- 2x Belt clamp nut holder
- 1x X carriage
- 2x Z motor mount
- 1x Extruder Idler
- 2x Coupling
- 3x Endstop holder
- 2x Pulley

----
Generated on 2011/12/03 00:41:02 by ThingDoc - http://thingdoc.org/

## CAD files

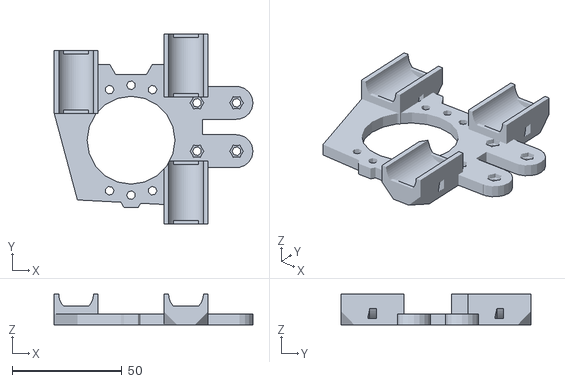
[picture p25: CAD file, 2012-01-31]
metric-prusa-lm8uu/x-carriage.stl
90.6 x 86.3 x 14.0

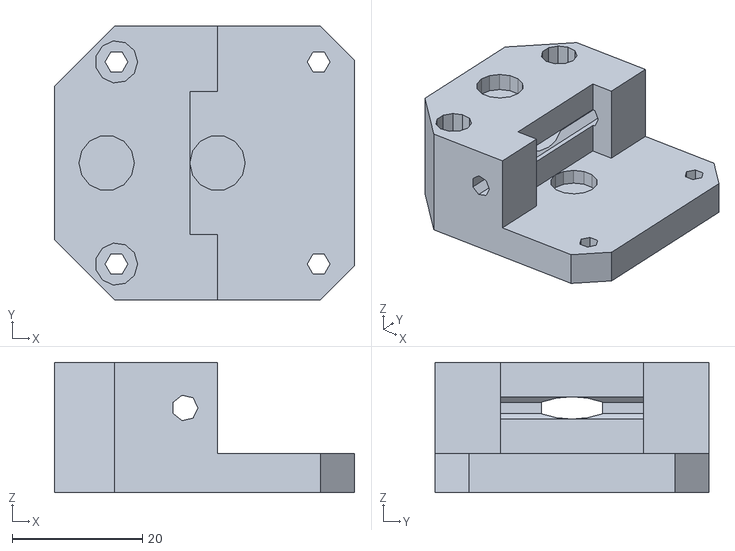
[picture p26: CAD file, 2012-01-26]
metric-prusa/experimental-extruder.stl
46.0 x 42.0 x 20.0

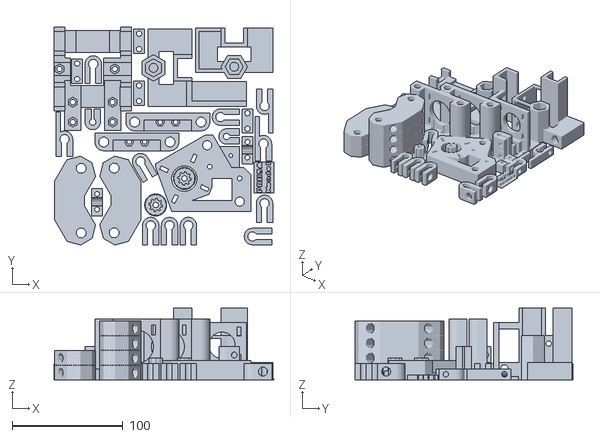
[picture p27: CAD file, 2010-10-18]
plate1.stl
199.0 x 197.2 x 65.1

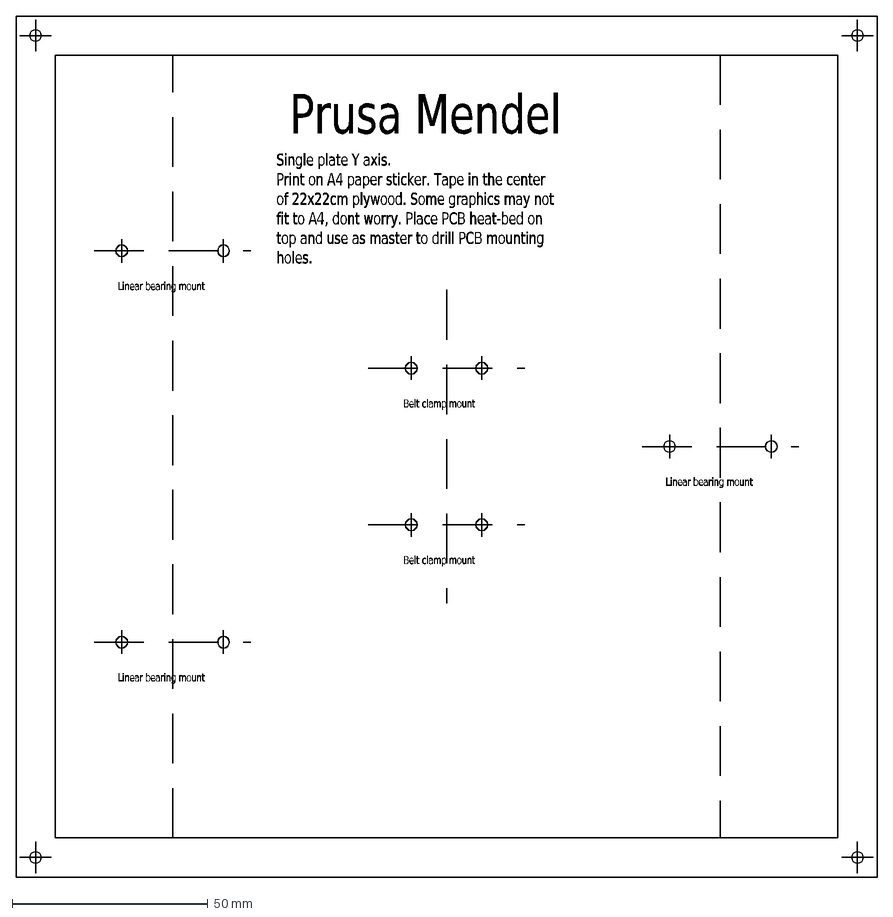
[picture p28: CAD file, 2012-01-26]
source/bed-drilling.dxf
Prusa\~Mendel
Single\~plate\~Y\~axis. Print\~on\~A4\~paper\~sticker.\~Tape\~in\~the\~center\~ of\~22x22cm\~plywood.\~Some\~graphics\~may\~not fit\~to\~A4,\~dont\~worry.\~Plac
Linear\~bearing\~mount
Belt\~clamp\~mount

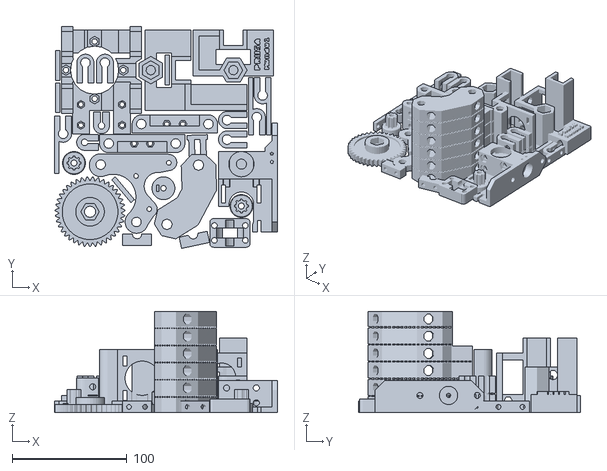
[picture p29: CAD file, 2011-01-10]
stl-sae/mendelplate.stl
194.5 x 193.5 x 88.3

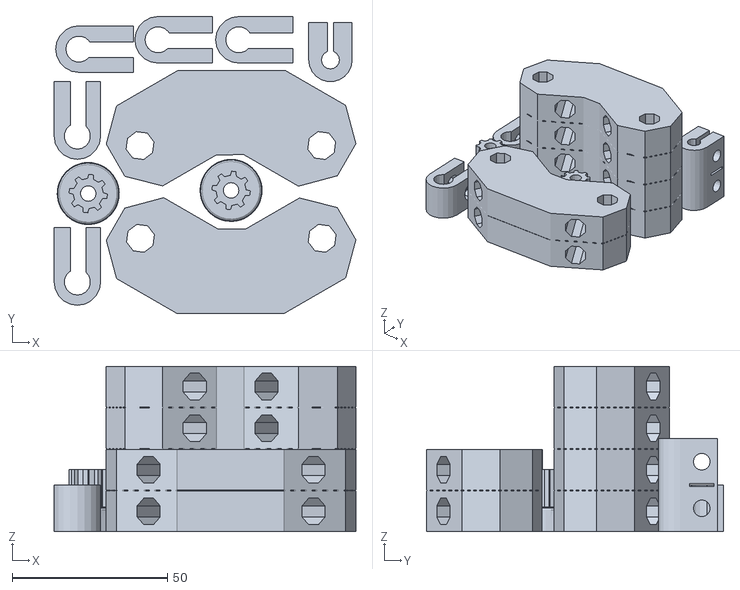
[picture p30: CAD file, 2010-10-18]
mbotplate1.stl
97.2 x 95.6 x 53.2

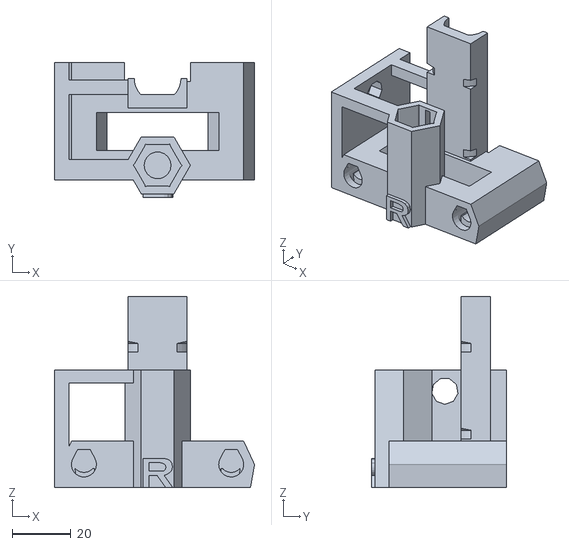
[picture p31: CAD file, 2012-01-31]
metric-prusa-lm8uu/x-end-idler.stl
67.9 x 46.0 x 65.0

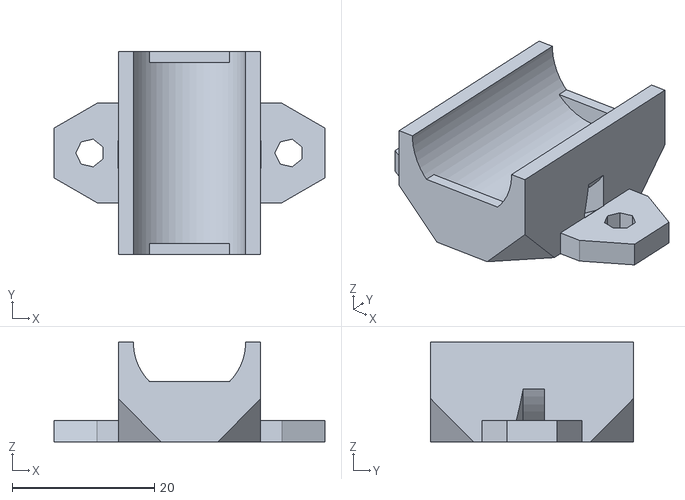
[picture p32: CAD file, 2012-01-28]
metric-prusa-lme8uu/y-bushing.stl
38.1 x 28.5 x 14.0

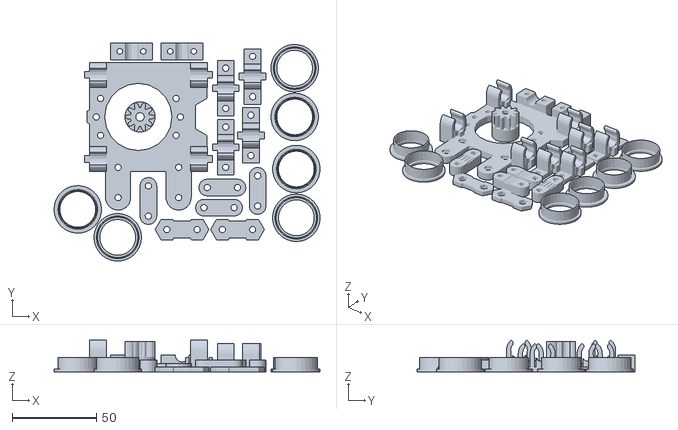
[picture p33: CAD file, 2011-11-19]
metric-prusa/mendel-plate-4.stl
158.2 x 129.7 x 19.0

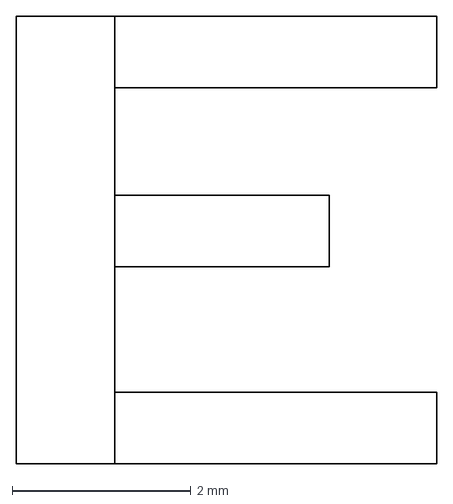
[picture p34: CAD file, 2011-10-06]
source/this-way-up.dxf
4.70 x 5.00 mm

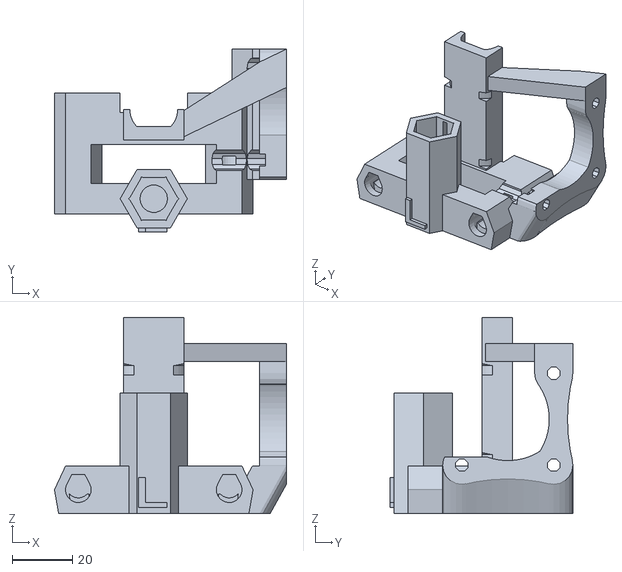
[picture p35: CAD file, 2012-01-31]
metric-prusa-lm8uu/x-end-motor.stl
76.9 x 60.6 x 65.0

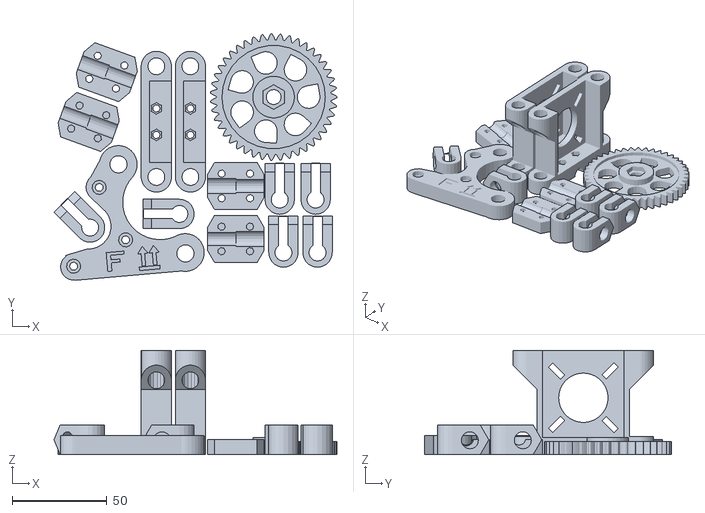
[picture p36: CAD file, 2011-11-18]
metric-prusa/mendel-plate-3.stl
149.6 x 130.3 x 55.0

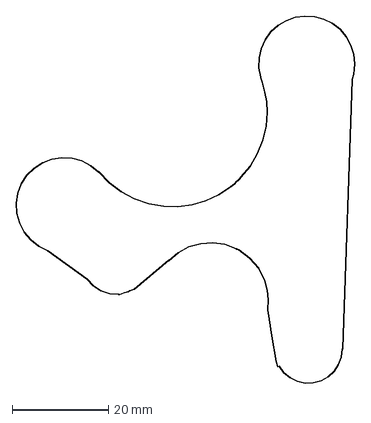
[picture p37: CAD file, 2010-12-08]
source/ybrac-t.dxf
70.5 x 76.4 mm

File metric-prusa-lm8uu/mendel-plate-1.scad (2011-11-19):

translate([34,140,0]) rotate([0,0,270]) import_stl("endstop-holder.stl");
translate([168,123,0]) rotate([0,0,90]) import_stl("bar-clamp.stl");
translate([71,120,0.0]) rotate([0,0,1890]) import_stl("x-end-motor.stl");
translate([135,120,0]) rotate([0,0,270]) import_stl("x-end-idler.stl");
translate([127,84,0]) rotate([0,0,180]) import_stl("wade.stl");
translate([46,86,0]) rotate([0,0,90]) import_stl("endstop-holder.stl");
translate([168,91,0]) rotate([0,0,90]) import_stl("bar-clamp.stl");
translate([152,46,0]) rotate([0,0,45]) import_stl("endstop-holder.stl");

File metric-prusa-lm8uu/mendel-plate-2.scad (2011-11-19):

translate([84,130,0]) rotate([0,0,150]) import_stl("frame-vertex-foot.stl");
translate([111,28,0]) rotate([0,0,75]) import_stl("frame-vertex-foot.stl");
translate([128,120,0]) rotate([0,0,125]) import_stl("frame-vertex-foot.stl");
translate([146,83,0]) rotate([0,0,35]) import_stl("frame-vertex.stl");
translate([124,50,0]) rotate([0,0,35]) import_stl("frame-vertex-foot.stl");
translate([100,79,0]) rotate([0,0,-110]) import_stl("frame-vertex.stl");

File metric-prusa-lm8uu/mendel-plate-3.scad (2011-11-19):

translate([50,58,0]) rotate([0,0,135]) import_stl("bar-clamp.stl");
translate([166,65,0]) rotate([0,0,90]) import_stl("bar-clamp.stl");
translate([43,127,0]) rotate([0,0,-20]) import_stl("coupling.stl");
translate([167,37,0]) rotate([0,0,90]) import_stl("bar-clamp.stl");
translate([61,62,0]) rotate([0,0,5]) import_stl("ybrac-t.stl");
translate([74,114,0]) rotate([0,0,0]) import_stl("z-motor-mount.stl");
translate([149,37,0]) rotate([0,0,90]) import_stl("bar-clamp.stl");
translate([147,65,0]) rotate([0,0,90]) import_stl("bar-clamp.stl");
translate([92,114,0]) rotate([0,0,0]) import_stl("z-motor-mount.stl");
translate([94,73,0]) rotate([0,0,-180]) import_stl("bar-clamp.stl");
translate([136,127,0]) rotate([0,0,0]) import_stl("wade-big.stl");
translate([116,66,0]) rotate([0,0,0]) import_stl("coupling.stl");

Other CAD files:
metric-prusa-lme8uu/x-carriage.stl
stl/mendelplate.stl
metric-prusa-lme8uu/x-end-idler.stl
metric-prusa-lme8uu/x-end-motor.stl
metric-prusa-lm8uu/mendel-plate-4.scad
metric-prusa-lm8uu/bar-clamp.stl
metric-prusa-lm8uu/bar-clamps.stl
metric-prusa-lm8uu/belt-clamp-bed-holder.stl
metric-prusa-lm8uu/belt-clamp.stl
metric-prusa-lm8uu/frame-vertex-foot.stl
metric-prusa-lm8uu/frame-vertex.stl
metric-prusa-lm8uu/igus-adapter.stl
metric-prusa-lm8uu/mendel-plate-1.stl
metric-prusa-lm8uu/mendel-plate-2.stl
metric-prusa-lm8uu/mendel-plate-3.stl
metric-prusa-lm8uu/mendel-plate-4.stl
metric-prusa-lm8uu/rod-clamp.stl
metric-prusa-lm8uu/wade-big.stl
metric-prusa-lm8uu/wade-small.stl
metric-prusa-lm8uu/wade.stl
metric-prusa-lm8uu/wadebits.stl
metric-prusa-lm8uu/z-motor-mount.stl
metric-prusa-lme8uu/bar-clamp.stl
metric-prusa-lme8uu/bearing-guide.stl
metric-prusa-lme8uu/belt-clamp-nut-holder.stl
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

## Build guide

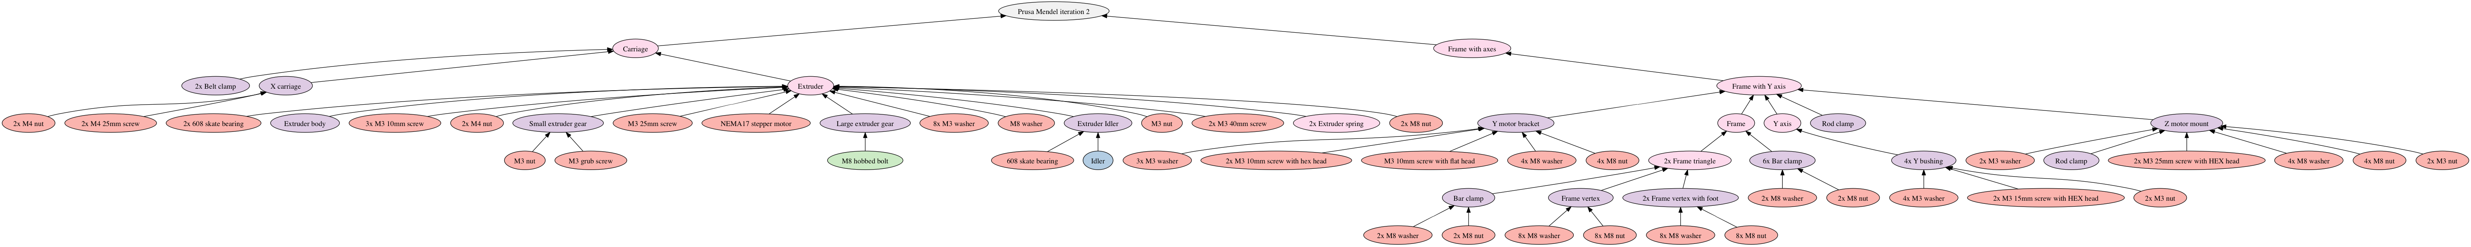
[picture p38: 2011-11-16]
docs/assembly-graph.png

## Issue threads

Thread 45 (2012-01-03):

BOM is far from complete

Shaun1, 2012-01-03:
Structural rods (with dimensions) , motors, gears etc. should be listed in BOM with adequate detail.

Closed 2021-11-27.

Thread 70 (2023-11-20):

MMU2S with Mk3S idler homing not working after firmware update. A solution!

hjvooijen, 2023-11-20:
As discussed in Github #4285 the MMU2S suffered idler homing problems.
The SW people were looking for solutions while changing sensitivity values.
I found that the motorshaft and Idlerdrum cannot be perfectly aligned. Also that the motor mount was not perfectly square to the Idler housing centerline.
My route as a mechanical engineer was to eliminate the over-determination .
Based on tolerances on the Idlerdrum connection to the motorshaft and the mounting plenum of the motor self, I changed the motor mount into one providing 2 extra rotation freedoms.
My machine is now working fine without any changes in sensitivity values with the latest firmware.
Read my doc please and try my .stl's on printables under MMU2S+ 🤭
I reach out to Prusa engineers to understand what I did and why.
For discussion available,
Henk van Ooijen

[MMU2S solution for firmware updates.pdf](https://github.com/josefprusa/PrusaMendel/files/13404699/MMU2S.solution.for.firmware.updates.pdf)

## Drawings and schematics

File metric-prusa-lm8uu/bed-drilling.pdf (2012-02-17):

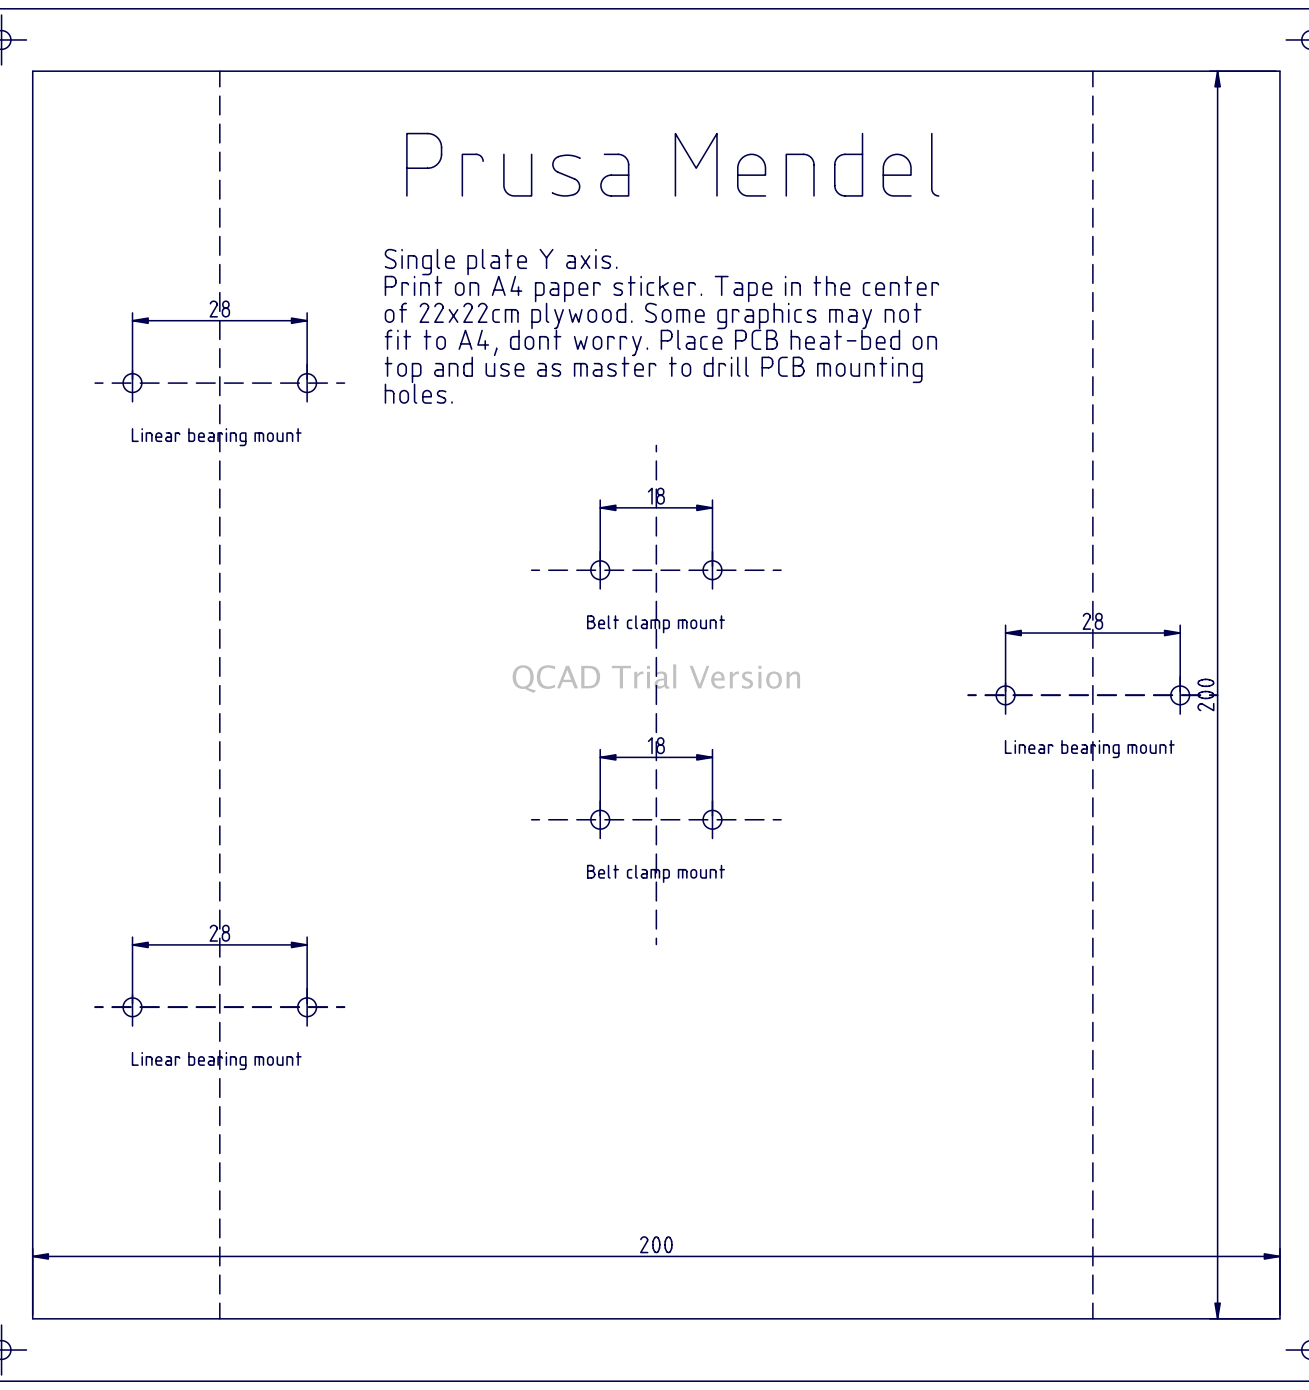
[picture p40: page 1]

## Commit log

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2010-09-15 Adding compatibility for BfB hotend
    [x-carriage.scad]
2010-10-04 Newer X axis with slimmer x-end parts and with carriage supporting horizontal mounting of extruder, also changed bushing holders to use with diy pla bushings. + Adding pla bushings to repo
    [pla-bushing.scad, pla-bushing.stl, x-carriage.scad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]
2010-10-06 Adding the slimmed vertexes, only STLs for now, OpenSCAD will follow!
    [viksVertexSlim.stl, viksVertexSlimFoot.stl]
2010-10-10 Fixed spacing for different diameters
    [pla-bushing.scad]
2010-10-12 Started README file. Added Frame-vertex parts.
    [frame-vertex-foot.stl, frame-vertex.scad, frame-vertex.stl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]
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2010-10-12 Better coupling which should take M8 rod without mod. I still have better idea in head tho ;-)
    [coupling.scad, coupling.stl]
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2010-10-13 Added plate and dependencies
    [plate1.scad, plate1.stl, prusalogo.scad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]
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2010-10-13 Added netfabb-optimized stl, thanks to SpaceXULA
    [plate1-netfabb.stl]
2010-10-16 Changed model so the raft does not disappear when skeining at 0.4mm layer size.
    [bar-clamp.stl, belt-clamp.stl]
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2010-10-20 Stacked vertices for raft testing
    [vertexstack.scad, vertextstack.stl]
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2010-10-20 Converted production plates to new raft type
    [makerbot.scad, plate1.scad]
2010-11-19 Parametrized all files. Changed pla-bushing to contain 12 bushings. Changed x-end-idler to M8 hole. New Y-motor-bracket (ybrac.scad). Repositioned rod-clamp to start at z=0.
    [bar-clamp.scad, belt-clamp.scad, coupling.scad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]
2010-11-24 Removed external stl dependencies Improved y bracket Simplified x-end scad files Parametrized all nonparametric files
    [bar-clamp.stl, configuration.scad, coupling.scad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]
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2010-11-26 New Mendel production plate and improvements to files
    [bar-clamp.scad, belt-clamp.scad, belt-clamp.stl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]
2010-11-27 New and improved Makerbot plates. They now fit on the platform without removing bolts.
    [makerbot.scad, mbotplate2.stl, mbotplate3.stl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]
2010-12-02 Fix a stupid mistake in the x carriage. Fix a nonparametric hole in the rod clamp. Update production plates.
    [configuration.scad, makerbot.scad, mbotplate2.stl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]
2010-12-06 Prepared configuration file to be able to handle multiple settings. Added settings for bushings.
    [configuration-metric.scad, configuration.scad]
2010-12-06 Helical bushings and off the shelf bushings holder.
    [pla-bushing.scad]
2010-12-06 Better WADE positioning on x-carriage
    [x-carriage.scad, x-carriage.stl]
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2010-12-10 Fixed hole spacing to be 58.5 instead of 60 so it matches the vertex
    [z-motor-mount.scad]
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2010-12-19 Adding makefile, minor fixes to parts.
    [frame-vertex.scad, makerbot.scad, wade.scad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]
2011-01-05 New Makefile with dependencies and parametric plate generation plus extruder and other fun stuff. Option for generating SAE bits with a single command-line change when calling make.
    [bar-clamp.stl, belt-clamp.stl, configuration.scad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]
2011-01-05 Plate1 now includes an extruder
    [plate1.scad]
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2011-01-05 Fixed makerbot plate 3
    [makerbot.scad, mbotplate3.stl]
2011-01-06 Fix the m3 holes on the pulleys and the y motor bracket to size m3 even in the SAE version.
    [mbotplate5.stl, mendelplate.stl, pulley.scad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]
2011-01-08 Added PDF with documentation. Noted all imported stuff etc.
    [parametric_involute_gear_v5.0.scad, pulley.scad, wadebits.scad]
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2011-01-09 Switched the x-carriage belt clamp holes to m3.
    [x-carriage.scad, x-carriage.stl]
2011-01-09 Switched the belt clamp to M3 to match x-carriage.
    [belt-clamp.scad, belt-clamp.stl]
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2011-01-10 Generated new plates with the m3-ification and SAE mendel plate
    [endstop-holder.stl, mbotplate2.stl, mbotplate3.stl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]
2011-01-10 Better endstopholder, wont snap if its printed in PLA.
    [endstop-holder.scad, endstop-holder.stl]
2011-01-13 NOPHEAD fixes. Tighter frame-vertex holes, tighter motor shaft couplings, motor shaft couplings positioned in the right way for better printing, fixed motor mounts to easier fit motors. (Need to rege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
    [belt-clamp.stl, configuration.scad, coupling.scad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]
2011-01-13 Added calibration object. TODO: write how to use it :-)
    [calibration.scad, calibration.stl]
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2011-01-14 Rounded corners and thin wall feature. Check out configuration for more info
    [configuration.scad, x-end-idler.scad, x-end-idler.stl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]
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2011-01-23 Modified pulley. Bigger nut entrance, longer teeth, easier assembly.
    [pulleymod.scad, pulleymod.stl]
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2011-01-23 New wade body - added nut traps to the bottom and mounting points for 30mm wide extra hotend holding bracket
    [wade.scad]
2011-02-05 Rebuilt SAE mendel with new settings from SpaceXULA
    [bar-clamp.stl, belt-clamp.stl, configuration.scad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]
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2011-02-15 renamed belt-clamps.jpg -> belt-clamp.jpg so that thingdoc can find it. updated doc.pdf and bom.txt by running thingdoc again. belt-clamp.jpg appears correctly in this pdf. so commit it too.
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2011-03-29 Regenerated all STLs, ready to merge into MASTER
    [bar-clamp.stl, belt-clamp.stl, calibration.stl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]
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2011-04-21 Fix footedness of frame-vertex to correctly read makefile variable.
    [frame-vertex.scad]
2011-04-21 Correct footedness for stl files
    [frame-vertex-with-foot.stl, frame-vertex-without-foot.stl]
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2011-05-02 Newest x-axis as on prusa junior build :-)
    [bushing.scad, x-carriage.scad, x-end-idler.scad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]
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2011-05-26 add missing IDs
    [bar-clamp.scad, belt-clamp.scad, bushing.scad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]
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2011-05-30 Added assembly info in ThingDOC format to gregstruder
    [printable-bushing.scad, wade.scad, wadebits.scad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]
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2011-08-03 Reverted to my x-end code, gregs caused problems
    [x-end-idler.scad, x-end-motor.scad, x-end.scad]
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2011-09-14 Fixed typos
    [sae.scad]
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2012-01-21 merged keegis changes for LME8UU and added a configuration switch
    [bushing.scad, configuration.scad]
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2012-01-24 removed zip-tie holes on x-carriage, should work as push-fit now
    [bushing.scad, x-carriage.stl]
2012-01-24 [WIP] more changes - need to check with lm8uu
    [bushing.scad, x-carriage.stl]
2012-01-26 Improved LM8UU version which will be the preferred one from now on.
    [bar-clamp.scad, bar-clamp.stl, bed-drilling.dxf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]
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2012-01-26 fixed x/y linear bearing hole size and made it a little bit stronger
    [bushing.scad, x-carriage.stl, x-end-idler.stl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]
2012-01-26 fix Z bar position on lme8uu holder
    [bushing.scad, x-carriage.stl, x-end-idler.stl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]
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2012-01-27 raised bar spacing a little more on Z bushings
    [bushing.scad, z_linear_test.stl]
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2012-01-27 added fixed lme8uu x-carriage
    [bushing.scad, x-carriage.stl]
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2012-01-27 done testing; rebuilt files for lm8uu and lme8uu
    [x-carriage.stl, x-end-idler.stl, x-end-motor.stl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]
2012-01-27 fixed x-end-idler structural support beam placement for new bearing holders, will fix x-end-motor next
    [x-end-idler.scad, x-end-idler.stl]
2012-01-28 fixed x-end-motor for zip-tie mount linear mount
    [x-end-motor.scad]
2012-01-28 added stl for fixed x-end-motor
    [x-end-motor.stl]
2012-01-28 set linear=false in configuration to not break the bushing file generator by default
    [configuration.scad]
2012-01-30 set lme8uu=false in generate-lm8uu file and re-generated lm8uu files
    [x-carriage.stl, x-end-idler.stl, x-end-motor.stl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]
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2012-02-08 smooth_bar_diameter = 0; Wrong spelling must be your czech "i"
    [configuration.scad]
2012-02-10 making the push fit holes slightly larger and add a taper entrance
    [x-end.scad]
2012-02-10 fixed another typo/bug 48
    [configuration.scad]
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2012-02-22 Fixed the bed drilling template
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
